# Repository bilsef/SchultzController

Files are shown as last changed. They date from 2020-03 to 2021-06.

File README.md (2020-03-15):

# SchultzController

G-code controller for Siemens S (Schultz) feeders

## Arduino based controller in the hardware section.

The controller board distributes power to the feeders and provides the communication interface for 20 feeder units (40 lanes of components).  There are two versions of the controller board.  The KiCad files are in this folder.
* The 4 pin version has 20 individual 4 pin connectors.  One for each feeder unit.
* the 96 pin version has one 96 pin DIN connector compatible with the connector on the Siemens Communication Unit connector board.  This board is Siemens 1710470-Y1032-C1-01-86 and is inside of 00316265S05.
 
## Arduino code in the firmware section.

The board uses a Arduino Nano Every.  This is a low cost arduino which can easily be soldered to the control board.  Edit the config.h file in the arduino sketch to select the type of board you are using, then upload the sketch to the board.

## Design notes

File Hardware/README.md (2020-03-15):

# Have the board built by JLCPCB.com

* Go to jlcpcb.com and select SMT Assembly->Quote Now.
* Upload the zip file from the CAM directory of the board you want to build.
* Leave everything as default.  Scroll down to SMT Assembly and click Assemble your PCB boards.
* Choose Assemble bottom side.
* Choose your quantity and click Confirm.
* Upload the BOM and POS xlsx files from the CAM directory.
* Click NEXT.
* Confirm the BOM, click NEXT.
* Confirm the parts placement. If the placement doesn't show up, don't worry about it.  It has been verified.  Click SAVE TO CART and complete your purchase.
* [Buy me a coffee](https://www.buymeacoffee.com/cbVmnqB):coffee::smile:
* After you receive your boards, solder on the Arduino Nano Every using the surface mount pads and castellated holes.  Add connectors of your choice.  The 4 pin layout was made for JST B4B-XH-A(LF)(SN) connectors, but any 2.5mm compatible connector should work.

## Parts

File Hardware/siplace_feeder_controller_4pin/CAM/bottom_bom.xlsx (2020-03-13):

Designator | Comment | Footprint | LCSC Part #
Q1 Q2 Q3 Q4 Q5 Q6 Q7 Q8 Q9 Q10 Q11 Q12 Q13 Q14 Q15 Q16 Q17 Q18 Q19 Q20 | BC846 | SOT-23 | C163723
Q21 Q22 Q23 Q24 Q25 Q26 Q27 Q28 Q29 Q30 Q41 Q42 Q43 Q44 Q45 Q46 Q47 Q48 Q49 Q50 | 2N7002 | SOT-23 | C181082
Q60 Q58 Q57 Q56 Q55 Q54 Q53 Q52 Q51 Q31 Q32 Q33 Q34 Q35 Q36 Q37 Q38 Q39 Q40 Q59 | BC856 | SOT-23 | C181145
R1 R2 R3 R4 R5 R6 R7 R8 R9 R10 R11 R12 R13 R27 R28 R29 R30 R31 R32 R33 | 4.7K | R_0603 | C23162
R14 R15 R16 R17 R18 R19 R20 R21 R22 R23 R24 R25 R26 R34 R35 R36 R37 R38 R39 R40 | 330 | R_0603 | C23138
R71 R70 R69 R68 R67 R66 R65 R64 R63 R62 R101 R92 R93 R94 R95 R96 R97 R98 R99 R100 | 1.2K | R_0603 | C22765
R83 R84 R85 R86 R87 R88 R89 R91 R61 R60 R59 R58 R57 R56 R55 R54 R53 R52 R90 R82 | 10K | R_0603 | C25804
R41 | 2.2K | R_0603 | C4190

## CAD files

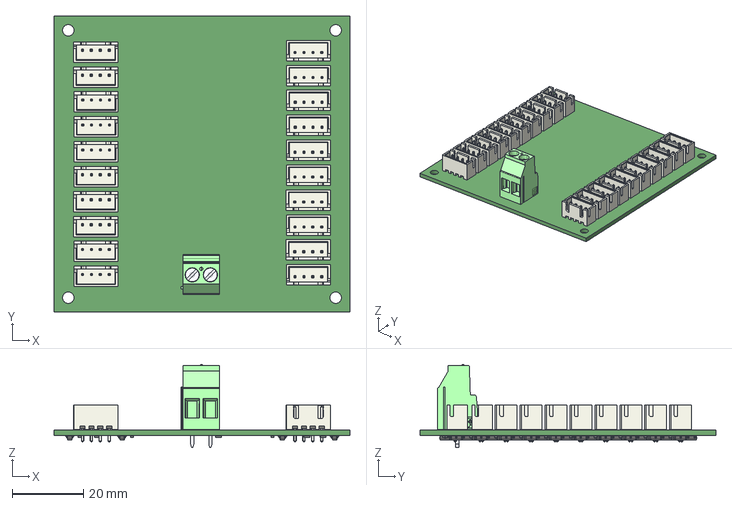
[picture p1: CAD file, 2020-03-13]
Hardware/siplace_feeder_controller_4pin/siplace_feeder_controller.step
83.0 x 83.0 x 23.3 mm

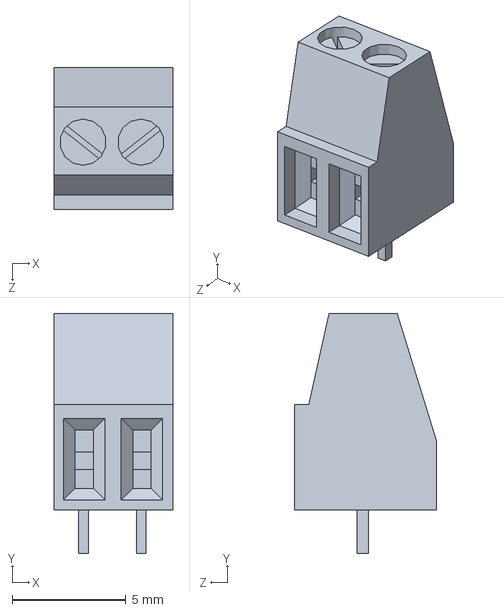
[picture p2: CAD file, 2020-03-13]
Hardware/siplace_feeder_controller_4pin/User Library-Connector-2.SLDPRT
5.22 x 10.5 x 6.22 mm

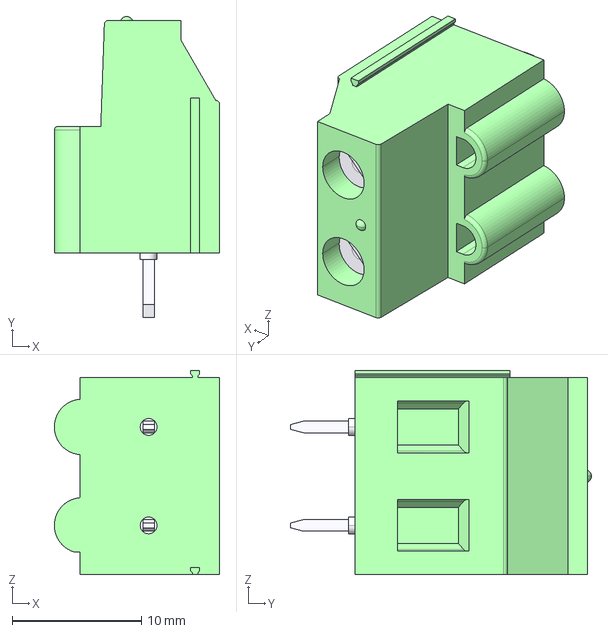
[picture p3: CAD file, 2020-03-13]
Hardware/siplace_feeder_controller_4pin/1732720.stp
12.8 x 23.3 x 15.8 mm

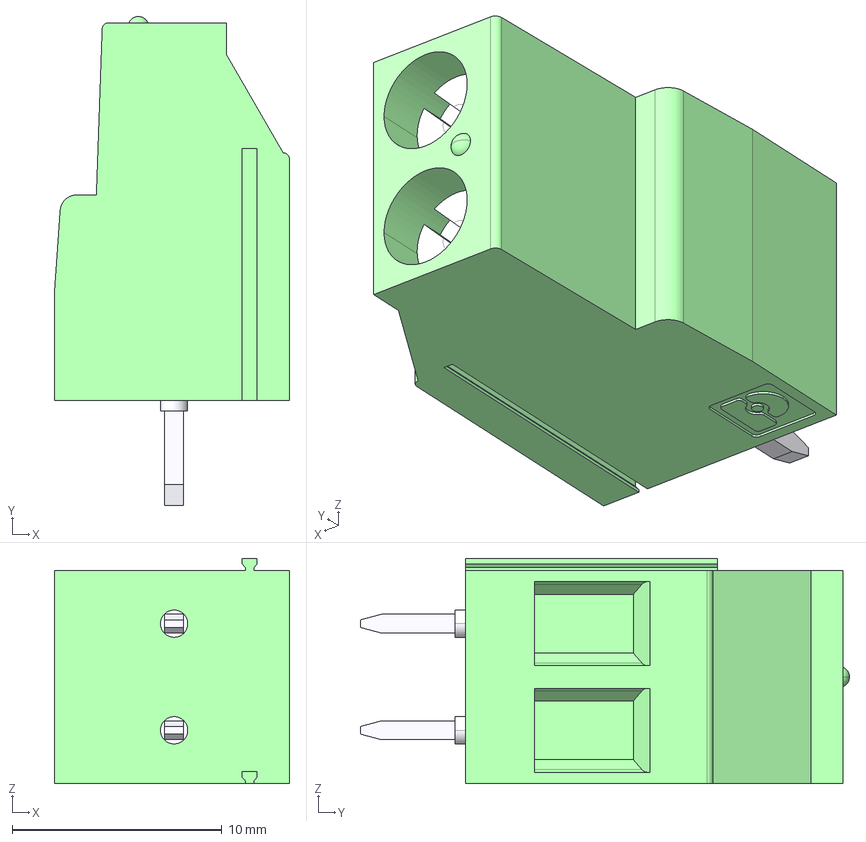
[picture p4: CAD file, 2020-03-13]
Hardware/siplace_feeder_controller_4pin/1706439.stp
11.2 x 23.3 x 10.7 mm

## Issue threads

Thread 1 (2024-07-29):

Compile issue to do library name.

Ccecil, 2024-07-29:
Using Arduino IDE ver. 1.8.19

Error due to missing library named "arduino.h".  Package now named "Arduino.h"

Easy fix but not immediately obvious.

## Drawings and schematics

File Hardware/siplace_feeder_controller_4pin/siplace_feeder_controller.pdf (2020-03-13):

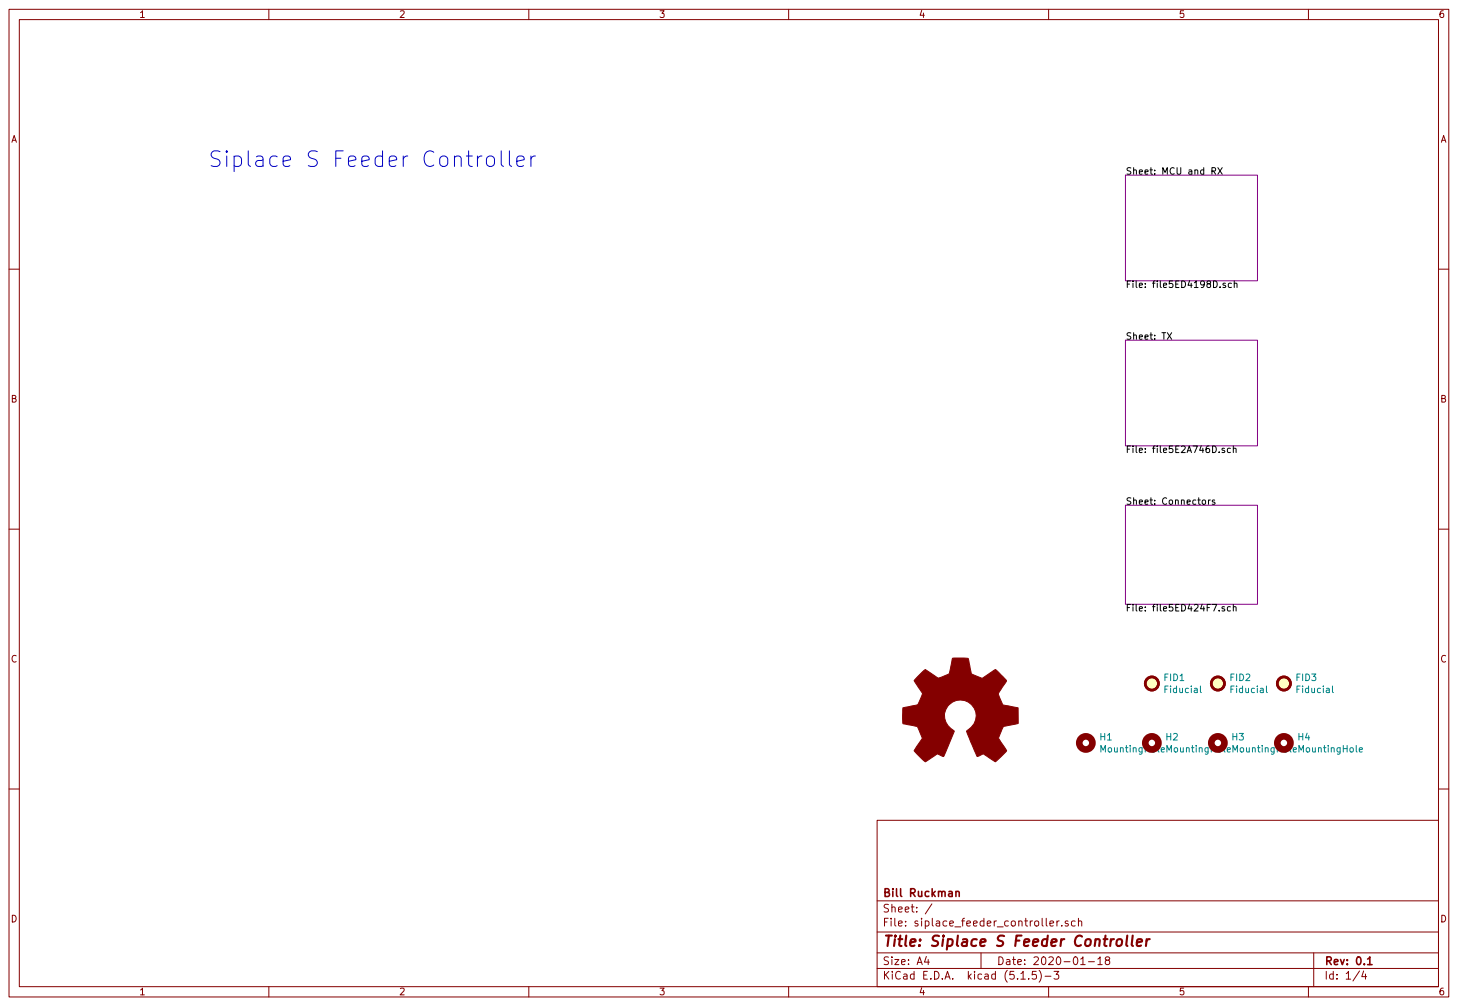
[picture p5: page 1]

Sheet: MCU and RX

File: file5ED4198D.sch Sheet: TX

File: siplace_feeder_controller.sch Sheet: / Bill Ruckman

Id: 1/4 Title: Siplace S Feeder Controller

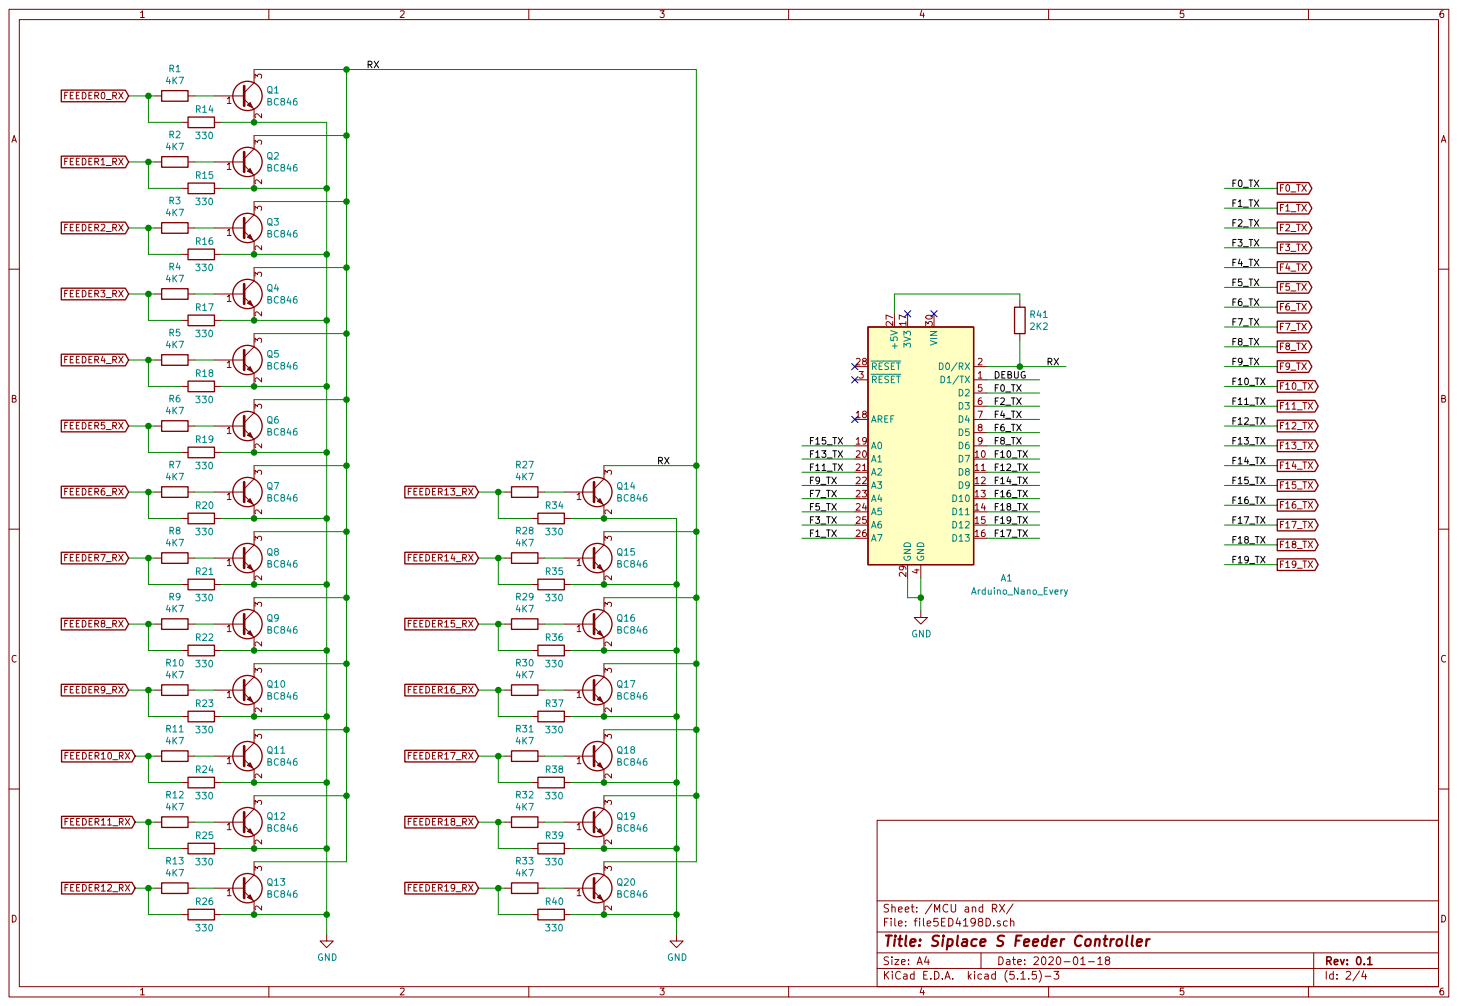
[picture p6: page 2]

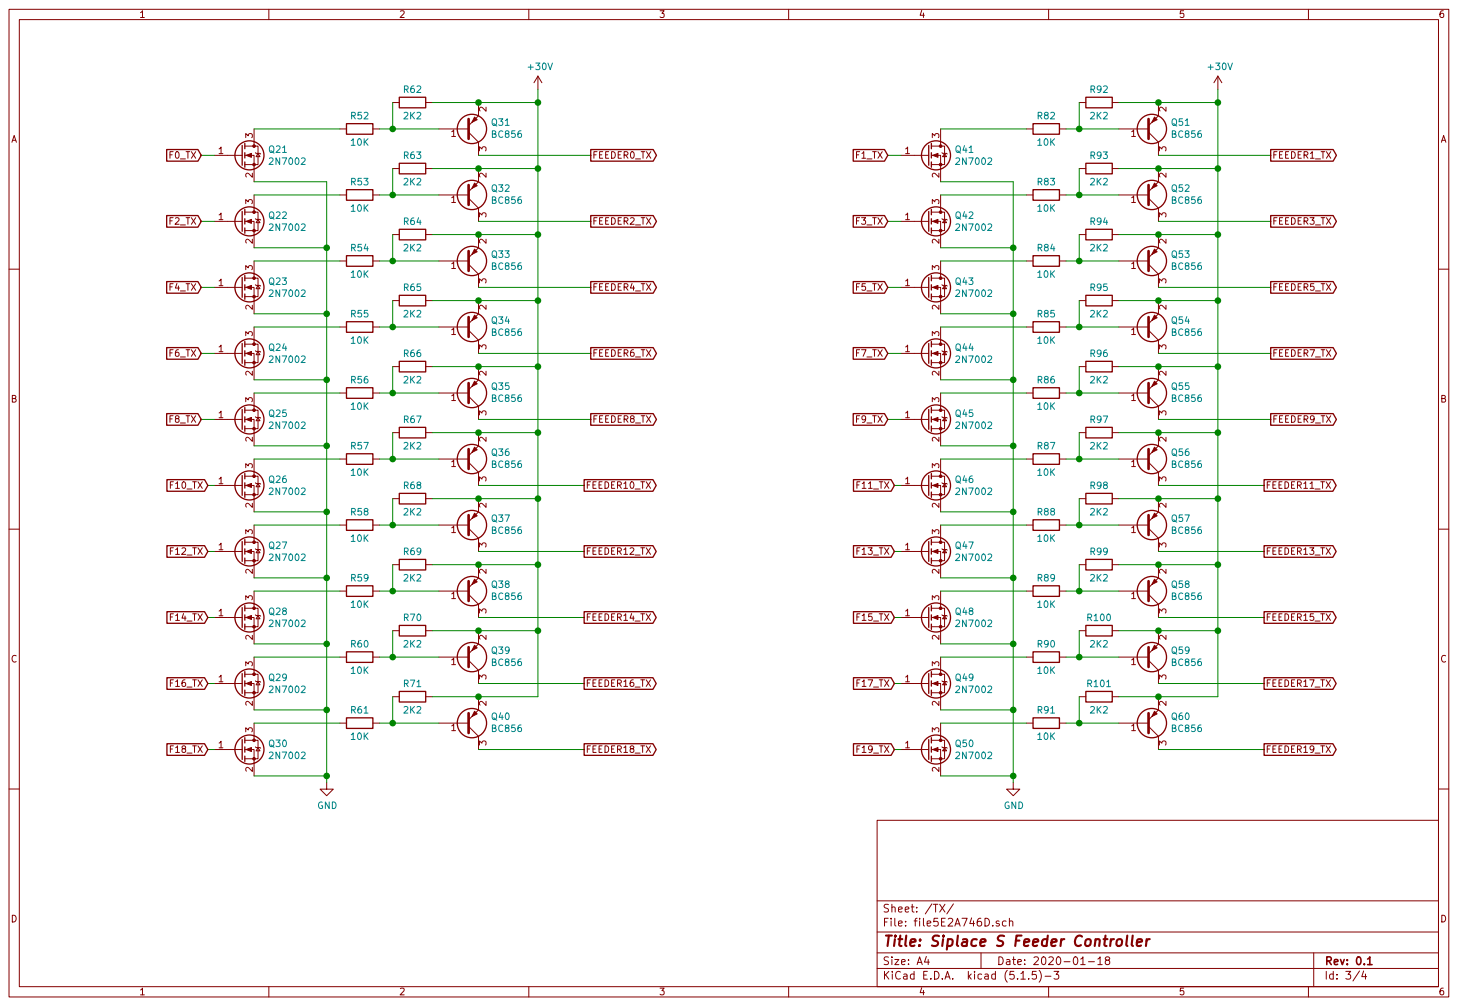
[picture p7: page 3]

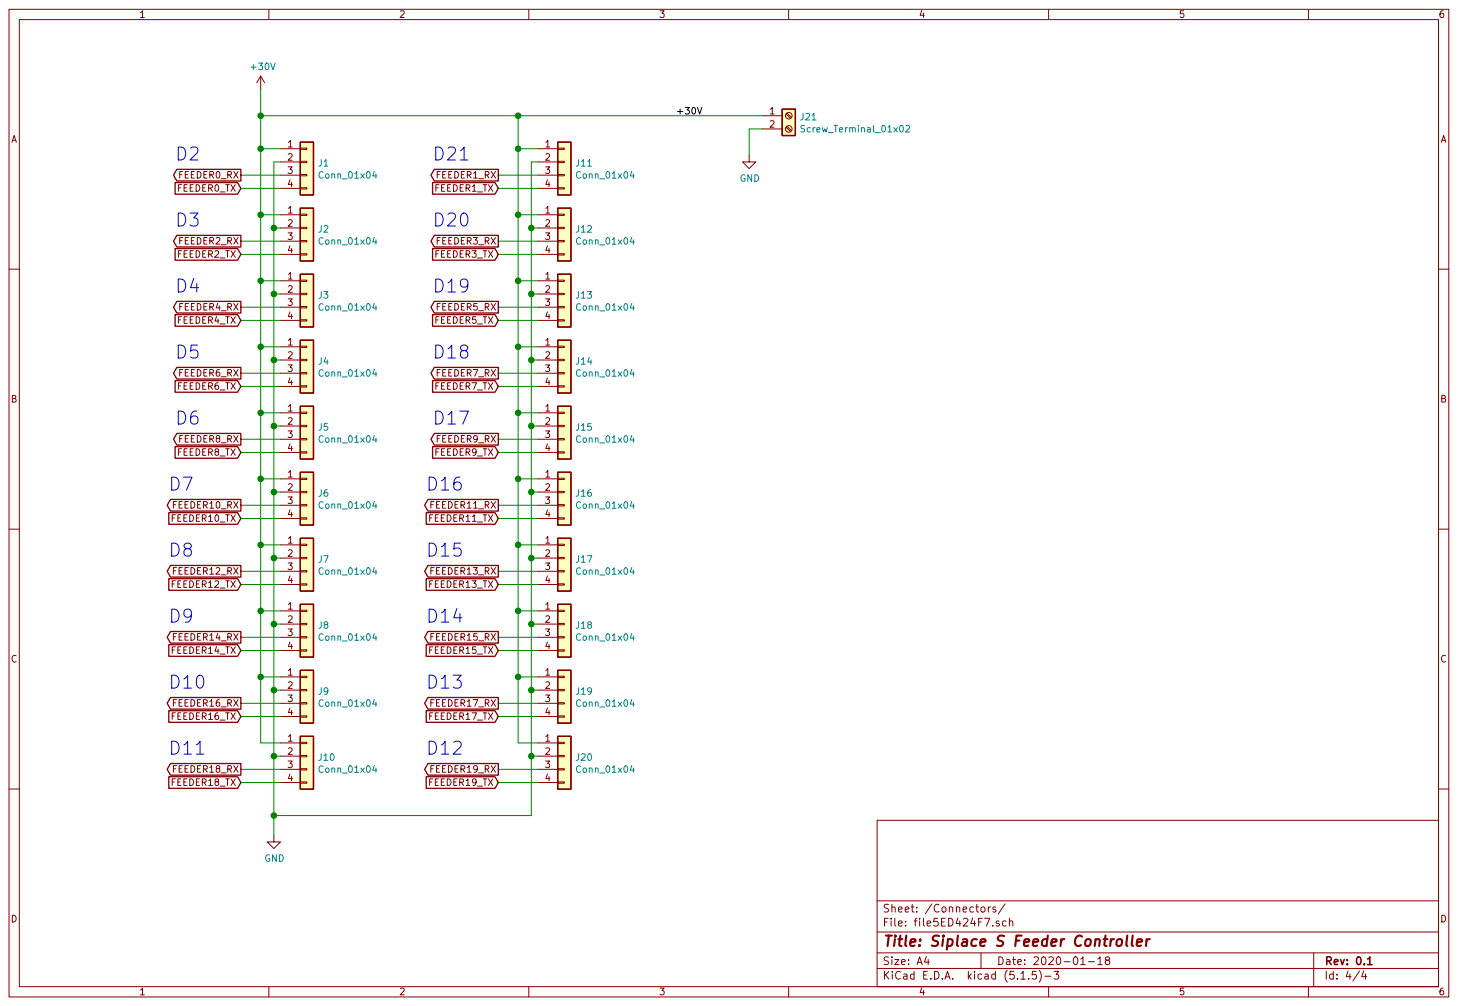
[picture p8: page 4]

Id: 4/4 Title: Siplace S Feeder Controller File: file5ED424F7.sch Sheet: /Connectors/ 1234

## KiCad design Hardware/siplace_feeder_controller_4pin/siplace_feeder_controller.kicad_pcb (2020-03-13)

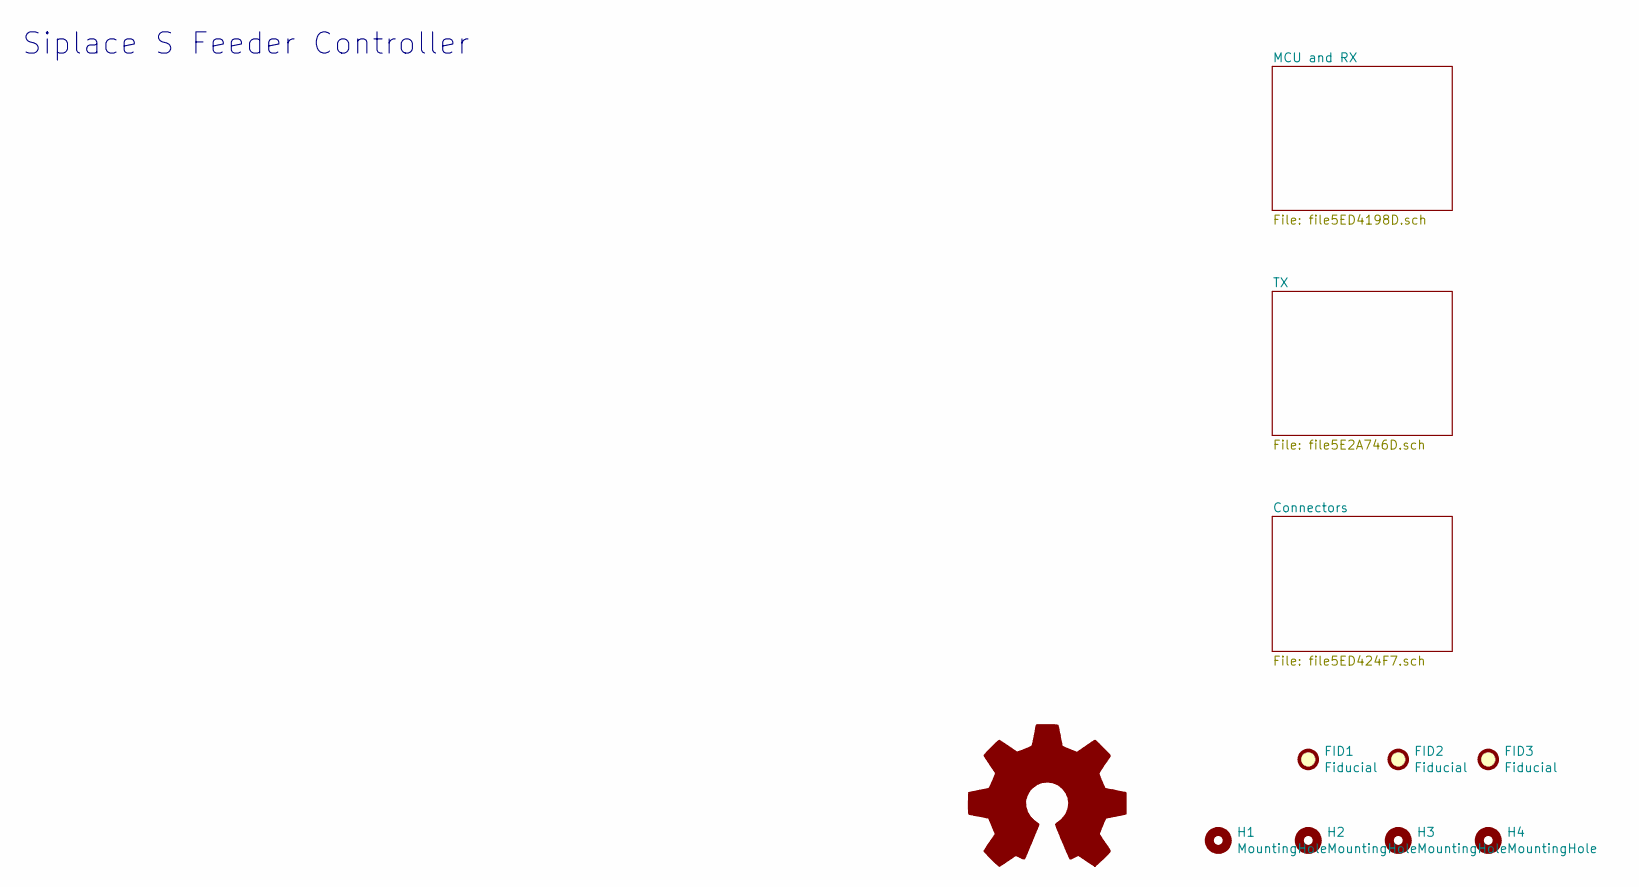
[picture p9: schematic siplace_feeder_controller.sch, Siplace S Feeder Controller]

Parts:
FID1, FID2, FID3: Fiducial; Fiducial_1mm_Mask3mm
H1, H2, H3, H4: MountingHole; MountingHole_3.2mm_M3

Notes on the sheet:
Siplace S Feeder Controller

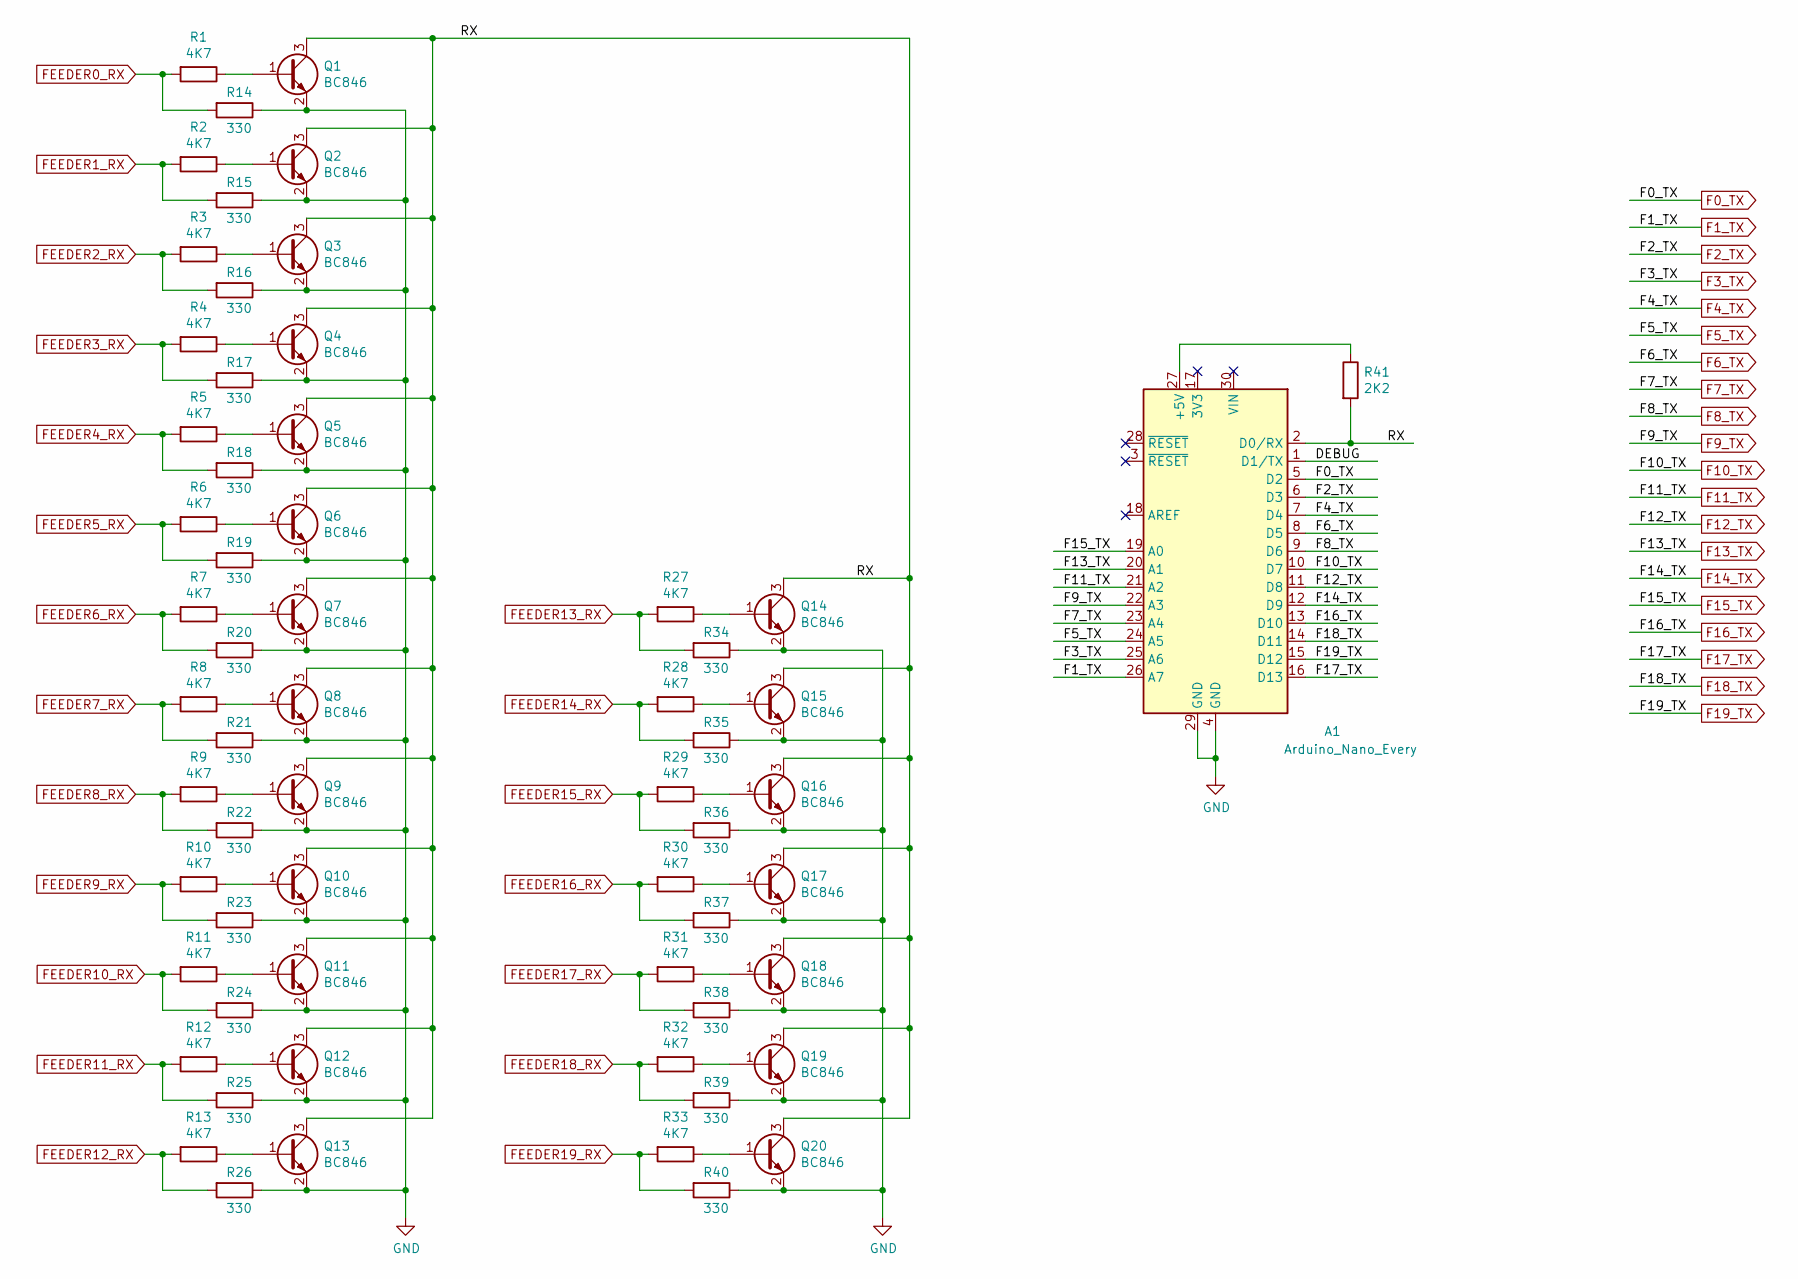
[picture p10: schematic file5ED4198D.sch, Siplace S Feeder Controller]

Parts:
A1: Arduino_Nano_Every; NANO_33_Footprint_SMD_Castell
Q1, Q2, Q3, Q4, Q5, Q6, Q7, Q8, Q9, Q10, Q11, Q12, Q13, Q14, Q15, Q16, Q17, Q18, Q19, Q20: BC846; SOT-23
R1, R2, R3, R4, R5, R6, R7, R8, R9, R10, R11, R12, R13, R27, R28, R29, R30, R31, R32, R33: 4K7; R_0603_1608Metric_Pad1.05x0.95mm_HandSolder
R14, R15, R16, R17, R18, R19, R20, R21, R22, R23, R24, R25, R26, R34, R35, R36, R37, R38, R39, R40: 330; R_0603_1608Metric_Pad1.05x0.95mm_HandSolder
R41: 2K2; R_0603_1608Metric_Pad1.05x0.95mm_HandSolder

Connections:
/MCU and RX/DEBUG: A1.1 (D1/TX)
/MCU and RX/RX: A1.2 (D0/RX), Q1.3 (C), Q2.3 (C), Q3.3 (C), Q4.3 (C), Q5.3 (C), Q6.3 (C), Q7.3 (C), Q8.3 (C), Q9.3 (C), Q10.3 (C), Q11.3 (C), Q12.3 (C), Q13.3 (C), Q14.3 (C), Q15.3 (C), Q16.3 (C), Q17.3 (C), Q18.3 (C), Q19.3 (C), Q20.3 (C), R41.2
F0_TX: A1.5 (D2); also elsewhere on the board
F1_TX: A1.26 (A7); also elsewhere on the board
F2_TX: A1.6 (D3); also elsewhere on the board
F3_TX: A1.25 (A6); also elsewhere on the board
F4_TX: A1.7 (D4); also elsewhere on the board
F5_TX: A1.24 (A5); also elsewhere on the board
F6_TX: A1.8 (D5); also elsewhere on the board
F7_TX: A1.23 (A4); also elsewhere on the board
F8_TX: A1.9 (D6); also elsewhere on the board
F9_TX: A1.22 (A3); also elsewhere on the board
F10_TX: A1.10 (D7); also elsewhere on the board
F11_TX: A1.21 (A2); also elsewhere on the board
F12_TX: A1.11 (D8); also elsewhere on the board
F13_TX: A1.20 (A1); also elsewhere on the board
F14_TX: A1.12 (D9); also elsewhere on the board
F15_TX: A1.19 (A0); also elsewhere on the board
F16_TX: A1.13 (D10); also elsewhere on the board
F17_TX: A1.16 (D13); also elsewhere on the board
F18_TX: A1.14 (D11); also elsewhere on the board
F19_TX: A1.15 (D12); also elsewhere on the board
FEEDER0_RX: R1.2, R14.2; also elsewhere on the board
FEEDER1_RX: R2.2, R15.2; also elsewhere on the board
FEEDER2_RX: R3.2, R16.2; also elsewhere on the board
FEEDER3_RX: R4.2, R17.2; also elsewhere on the board
FEEDER4_RX: R5.2, R18.2; also elsewhere on the board
FEEDER5_RX: R6.2, R19.2; also elsewhere on the board
FEEDER6_RX: R7.2, R20.2; also elsewhere on the board
FEEDER7_RX: R8.2, R21.2; also elsewhere on the board
FEEDER8_RX: R9.2, R22.2; also elsewhere on the board
FEEDER9_RX: R10.2, R23.2; also elsewhere on the board
FEEDER10_RX: R11.2, R24.2; also elsewhere on the board
FEEDER11_RX: R12.2, R25.2; also elsewhere on the board
FEEDER12_RX: R13.2, R26.2; also elsewhere on the board
FEEDER13_RX: R27.2, R34.2; also elsewhere on the board
FEEDER14_RX: R28.2, R35.2; also elsewhere on the board
FEEDER15_RX: R29.2, R36.2; also elsewhere on the board
FEEDER16_RX: R30.2, R37.2; also elsewhere on the board
FEEDER17_RX: R31.2, R38.2; also elsewhere on the board
FEEDER18_RX: R32.2, R39.2; also elsewhere on the board
FEEDER19_RX: R33.2, R40.2; also elsewhere on the board
GND: A1.4 (GND), A1.29 (GND), Q1.2 (E), Q2.2 (E), Q3.2 (E), Q4.2 (E), Q5.2 (E), Q6.2 (E), Q7.2 (E), Q8.2 (E), Q9.2 (E), Q10.2 (E), Q11.2 (E), Q12.2 (E), Q13.2 (E), Q14.2 (E), Q15.2 (E), Q16.2 (E), Q17.2 (E), Q18.2 (E), Q19.2 (E), Q20.2 (E), R14.1, R15.1, R16.1, R17.1, R18.1, R19.1, R20.1, R21.1, R22.1, R23.1, R24.1, R25.1, R26.1, R34.1, R35.1, R36.1, R37.1, R38.1, R39.1, R40.1; also elsewhere on the board
unnamed: A1.27 (+5V), R41.1
unnamed: Q1.1 (B), R1.1
unnamed: Q2.1 (B), R2.1
unnamed: Q3.1 (B), R3.1
unnamed: Q4.1 (B), R4.1
unnamed: Q5.1 (B), R5.1
unnamed: Q6.1 (B), R6.1
unnamed: Q7.1 (B), R7.1
unnamed: Q8.1 (B), R8.1
unnamed: Q9.1 (B), R9.1
unnamed: Q10.1 (B), R10.1
unnamed: Q11.1 (B), R11.1
unnamed: Q12.1 (B), R12.1
unnamed: Q13.1 (B), R13.1
unnamed: Q14.1 (B), R27.1
unnamed: Q15.1 (B), R28.1
unnamed: Q16.1 (B), R29.1
unnamed: Q17.1 (B), R30.1
unnamed: Q18.1 (B), R31.1
unnamed: Q19.1 (B), R32.1
unnamed: Q20.1 (B), R33.1

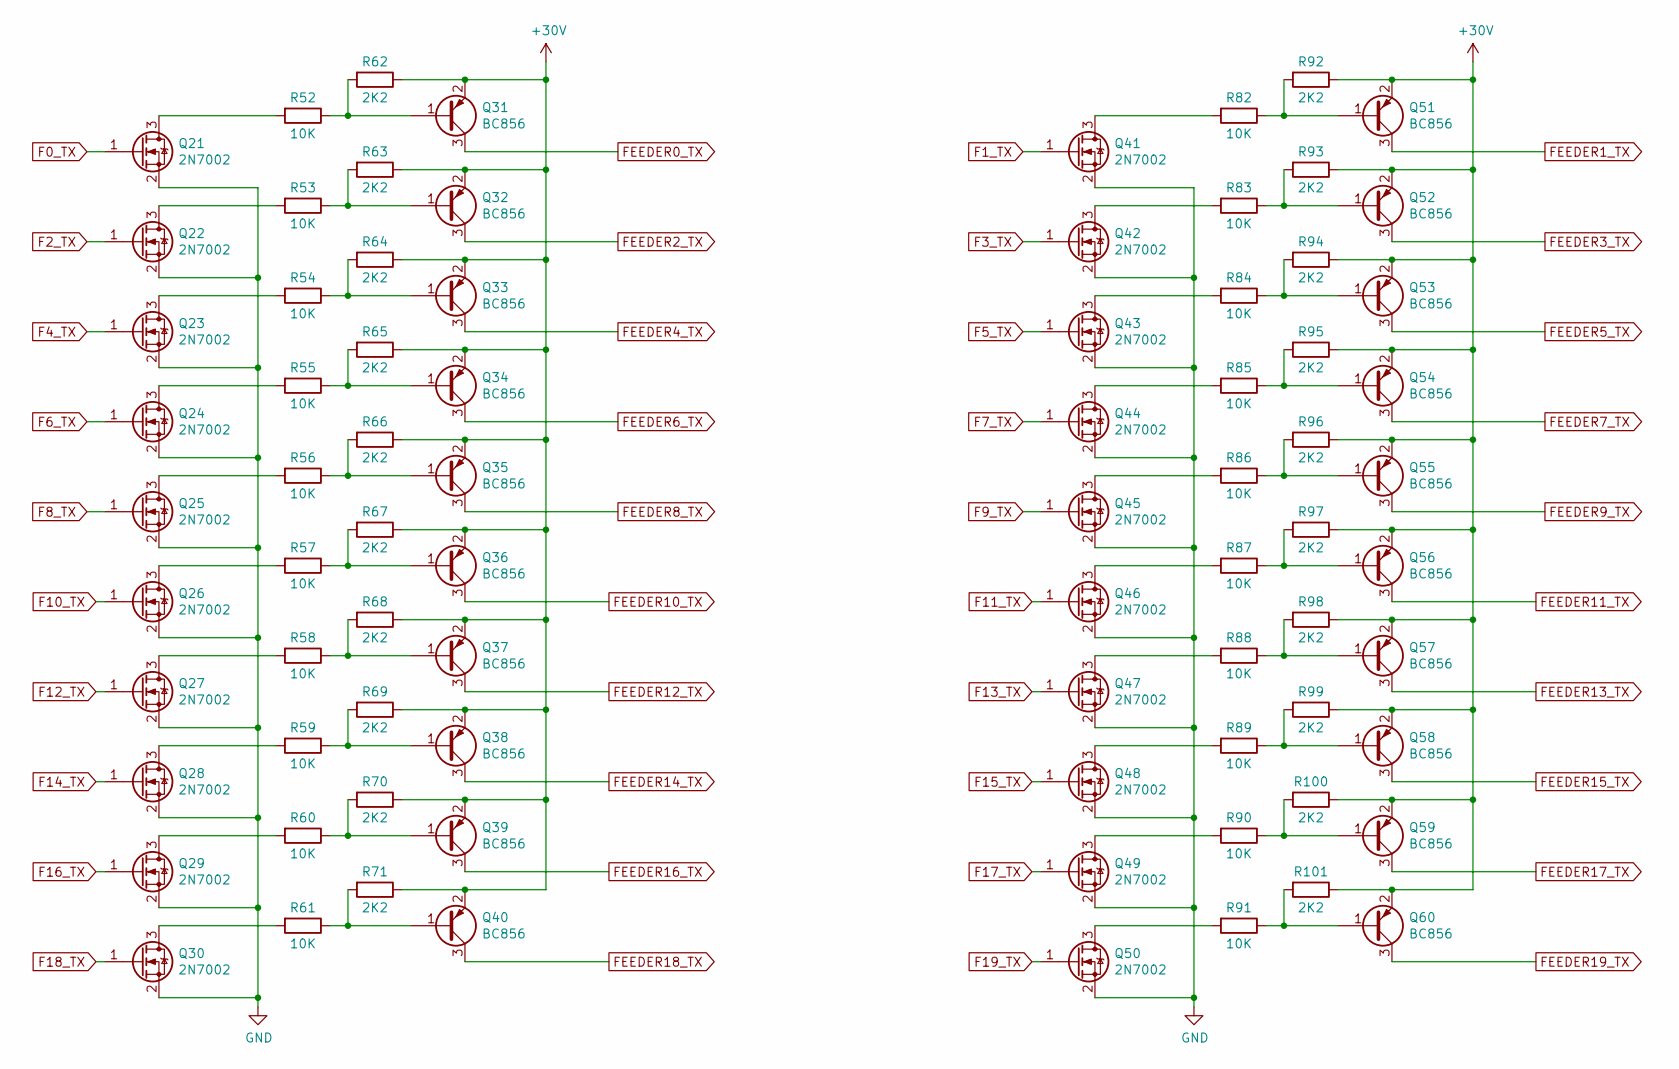
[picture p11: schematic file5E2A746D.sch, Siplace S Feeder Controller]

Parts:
Q21, Q22, Q23, Q24, Q25, Q26, Q27, Q28, Q29, Q30, Q41, Q42, Q43, Q44, Q45, Q46, Q47, Q48, Q49, Q50: 2N7002; SOT-23
Q31, Q32, Q33, Q34, Q35, Q36, Q37, Q38, Q39, Q40, Q51, Q52, Q53, Q54, Q55, Q56, Q57, Q58, Q59, Q60: BC856; SOT-23
R52, R53, R54, R55, R56, R57, R58, R59, R60, R61, R82, R83, R84, R85, R86, R87, R88, R89, R90, R91: 10K; R_0603_1608Metric_Pad1.05x0.95mm_HandSolder
R62, R63, R64, R65, R66, R67, R68, R69, R70, R71, R92, R93, R94, R95, R96, R97, R98, R99, R100, R101: 2K2; R_0603_1608Metric_Pad1.05x0.95mm_HandSolder

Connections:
+30V: Q31.2 (E), Q32.2 (E), Q33.2 (E), Q34.2 (E), Q35.2 (E), Q36.2 (E), Q37.2 (E), Q38.2 (E), Q39.2 (E), Q40.2 (E), Q51.2 (E), Q52.2 (E), Q53.2 (E), Q54.2 (E), Q55.2 (E), Q56.2 (E), Q57.2 (E), Q58.2 (E), Q59.2 (E), Q60.2 (E), R62.1, R63.1, R64.1, R65.1, R66.1, R67.1, R68.1, R69.1, R70.1, R71.1, R92.1, R93.1, R94.1, R95.1, R96.1, R97.1, R98.1, R99.1, R100.1, R101.1; also elsewhere on the board
F0_TX: Q21.1 (G); also elsewhere on the board
F1_TX: Q41.1 (G); also elsewhere on the board
F2_TX: Q22.1 (G); also elsewhere on the board
F3_TX: Q42.1 (G); also elsewhere on the board
F4_TX: Q23.1 (G); also elsewhere on the board
F5_TX: Q43.1 (G); also elsewhere on the board
F6_TX: Q24.1 (G); also elsewhere on the board
F7_TX: Q44.1 (G); also elsewhere on the board
F8_TX: Q25.1 (G); also elsewhere on the board
F9_TX: Q45.1 (G); also elsewhere on the board
F10_TX: Q26.1 (G); also elsewhere on the board
F11_TX: Q46.1 (G); also elsewhere on the board
F12_TX: Q27.1 (G); also elsewhere on the board
F13_TX: Q47.1 (G); also elsewhere on the board
F14_TX: Q28.1 (G); also elsewhere on the board
F15_TX: Q48.1 (G); also elsewhere on the board
F16_TX: Q29.1 (G); also elsewhere on the board
F17_TX: Q49.1 (G); also elsewhere on the board
F18_TX: Q30.1 (G); also elsewhere on the board
F19_TX: Q50.1 (G); also elsewhere on the board
FEEDER0_TX: Q31.3 (C); also elsewhere on the board
FEEDER1_TX: Q51.3 (C); also elsewhere on the board
FEEDER2_TX: Q32.3 (C); also elsewhere on the board
FEEDER3_TX: Q52.3 (C); also elsewhere on the board
FEEDER4_TX: Q33.3 (C); also elsewhere on the board
FEEDER5_TX: Q53.3 (C); also elsewhere on the board
FEEDER6_TX: Q34.3 (C); also elsewhere on the board
FEEDER7_TX: Q54.3 (C); also elsewhere on the board
FEEDER8_TX: Q35.3 (C); also elsewhere on the board
FEEDER9_TX: Q55.3 (C); also elsewhere on the board
FEEDER10_TX: Q36.3 (C); also elsewhere on the board
FEEDER11_TX: Q56.3 (C); also elsewhere on the board
FEEDER12_TX: Q37.3 (C); also elsewhere on the board
FEEDER13_TX: Q57.3 (C); also elsewhere on the board
FEEDER14_TX: Q38.3 (C); also elsewhere on the board
FEEDER15_TX: Q58.3 (C); also elsewhere on the board
FEEDER16_TX: Q39.3 (C); also elsewhere on the board
FEEDER17_TX: Q59.3 (C); also elsewhere on the board
FEEDER18_TX: Q40.3 (C); also elsewhere on the board
FEEDER19_TX: Q60.3 (C); also elsewhere on the board
GND: Q21.2 (S), Q22.2 (S), Q23.2 (S), Q24.2 (S), Q25.2 (S), Q26.2 (S), Q27.2 (S), Q28.2 (S), Q29.2 (S), Q30.2 (S), Q41.2 (S), Q42.2 (S), Q43.2 (S), Q44.2 (S), Q45.2 (S), Q46.2 (S), Q47.2 (S), Q48.2 (S), Q49.2 (S), Q50.2 (S); also elsewhere on the board
unnamed: Q21.3 (D), R52.2
unnamed: Q22.3 (D), R53.2
unnamed: Q23.3 (D), R54.2
unnamed: Q24.3 (D), R55.2
unnamed: Q25.3 (D), R56.2
unnamed: Q26.3 (D), R57.2
unnamed: Q27.3 (D), R58.2
unnamed: Q28.3 (D), R59.2
unnamed: Q29.3 (D), R60.2
unnamed: Q30.3 (D), R61.2
unnamed: Q31.1 (B), R52.1, R62.2
unnamed: Q32.1 (B), R53.1, R63.2
unnamed: Q33.1 (B), R54.1, R64.2
unnamed: Q34.1 (B), R55.1, R65.2
unnamed: Q35.1 (B), R56.1, R66.2
unnamed: Q36.1 (B), R57.1, R67.2
unnamed: Q37.1 (B), R58.1, R68.2
unnamed: Q38.1 (B), R59.1, R69.2
unnamed: Q39.1 (B), R60.1, R70.2
unnamed: Q40.1 (B), R61.1, R71.2
unnamed: Q41.3 (D), R82.2
unnamed: Q42.3 (D), R83.2
unnamed: Q43.3 (D), R84.2
unnamed: Q44.3 (D), R85.2
unnamed: Q45.3 (D), R86.2
unnamed: Q46.3 (D), R87.2
unnamed: Q47.3 (D), R88.2
unnamed: Q48.3 (D), R89.2
unnamed: Q49.3 (D), R90.2
unnamed: Q50.3 (D), R91.2
unnamed: Q51.1 (B), R82.1, R92.2
unnamed: Q52.1 (B), R83.1, R93.2
unnamed: Q53.1 (B), R84.1, R94.2
unnamed: Q54.1 (B), R85.1, R95.2
unnamed: Q55.1 (B), R86.1, R96.2
unnamed: Q56.1 (B), R87.1, R97.2
unnamed: Q57.1 (B), R88.1, R98.2
unnamed: Q58.1 (B), R89.1, R99.2
unnamed: Q59.1 (B), R90.1, R100.2
unnamed: Q60.1 (B), R91.1, R101.2

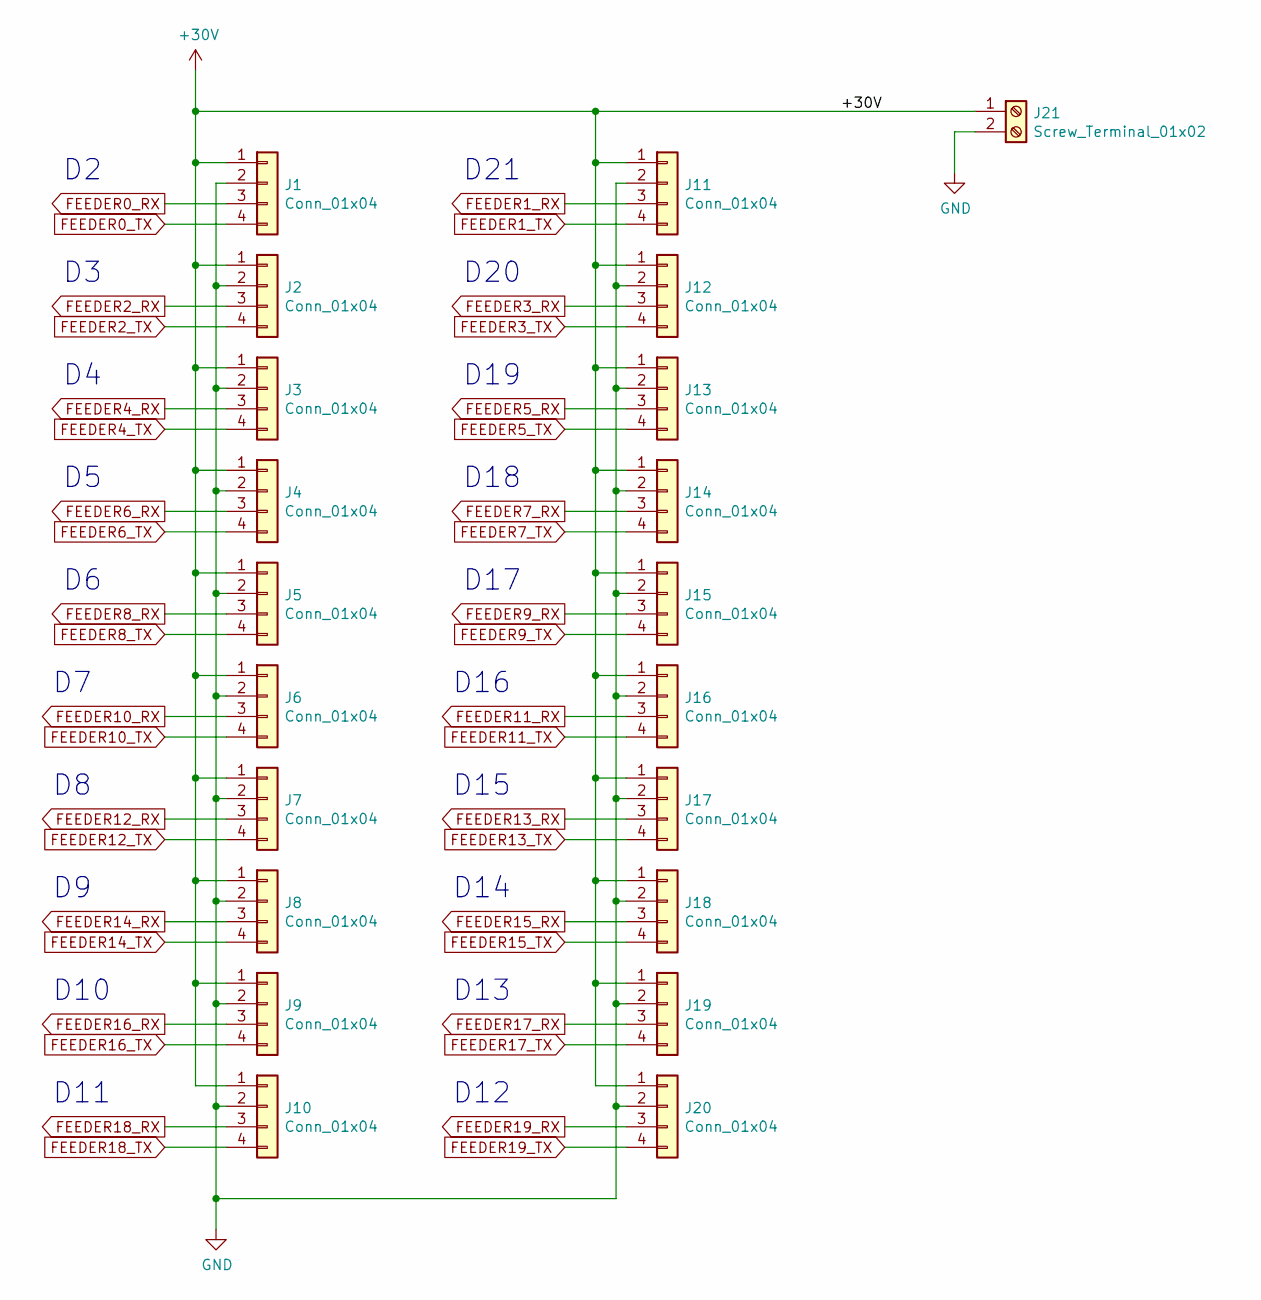
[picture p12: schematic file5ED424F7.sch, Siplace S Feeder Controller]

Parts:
J1, J2, J3, J4, J5, J6, J7, J8, J9, J10, J11, J12, J13, J14, J15, J16, J17, J18, J19, J20: Conn_01x04; JST_XH_B4B-XH-A_1x04_P2.50mm_Vertical
J21: Screw_Terminal_01x02; TerminalBlock_Phoenix_MKDS-1,5-2-5.08_1x02_P5.08mm_Horizont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

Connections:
+30V: J1.1, J2.1, J3.1, J4.1, J5.1, J6.1, J7.1, J8.1, J9.1, J10.1, J11.1, J12.1, J13.1, J14.1, J15.1, J16.1, J17.1, J18.1, J19.1, J20.1, J21.1; also elsewhere on the board
FEEDER0_RX: J1.3; also elsewhere on the board
FEEDER0_TX: J1.4; also elsewhere on the board
FEEDER1_RX: J11.3; also elsewhere on the board
FEEDER1_TX: J11.4; also elsewhere on the board
FEEDER2_RX: J2.3; also elsewhere on the board
FEEDER2_TX: J2.4; also elsewhere on the board
FEEDER3_RX: J12.3; also elsewhere on the board
FEEDER3_TX: J12.4; also elsewhere on the board
FEEDER4_RX: J3.3; also elsewhere on the board
FEEDER4_TX: J3.4; also elsewhere on the board
FEEDER5_RX: J13.3; also elsewhere on the board
FEEDER5_TX: J13.4; also elsewhere on the board
FEEDER6_RX: J4.3; also elsewhere on the board
FEEDER6_TX: J4.4; also elsewhere on the board
FEEDER7_RX: J14.3; also elsewhere on the board
FEEDER7_TX: J14.4; also elsewhere on the board
FEEDER8_RX: J5.3; also elsewhere on the board
FEEDER8_TX: J5.4; also elsewhere on the board
FEEDER9_RX: J15.3; also elsewhere on the board
FEEDER9_TX: J15.4; also elsewhere on the board
FEEDER10_RX: J6.3; also elsewhere on the board
FEEDER10_TX: J6.4; also elsewhere on the board
FEEDER11_RX: J16.3; also elsewhere on the board
FEEDER11_TX: J16.4; also elsewhere on the board
FEEDER12_RX: J7.3; also elsewhere on the board
FEEDER12_TX: J7.4; also elsewhere on the board
FEEDER13_RX: J17.3; also elsewhere on the board
FEEDER13_TX: J17.4; also elsewhere on the board
FEEDER14_RX: J8.3; also elsewhere on the board
FEEDER14_TX: J8.4; also elsewhere on the board
FEEDER15_RX: J18.3; also elsewhere on the board
FEEDER15_TX: J18.4; also elsewhere on the board
FEEDER16_RX: J9.3; also elsewhere on the board
FEEDER16_TX: J9.4; also elsewhere on the board
FEEDER17_RX: J19.3; also elsewhere on the board
FEEDER17_TX: J19.4; also elsewhere on the board
FEEDER18_RX: J10.3; also elsewhere on the board
FEEDER18_TX: J10.4; also elsewhere on the board
FEEDER19_RX: J20.3; also elsewhere on the board
FEEDER19_TX: J20.4; also elsewhere on the board
GND: J1.2, J2.2, J3.2, J4.2, J5.2, J6.2, J7.2, J8.2, J9.2, J10.2, J11.2, J12.2, J13.2, J14.2, J15.2, J16.2, J17.2, J18.2, J19.2, J20.2, J21.2; also elsewhere on the board

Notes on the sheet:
D21
D10
D11
D20
D19
D18
D17
D16
D15
D14
D13
D12

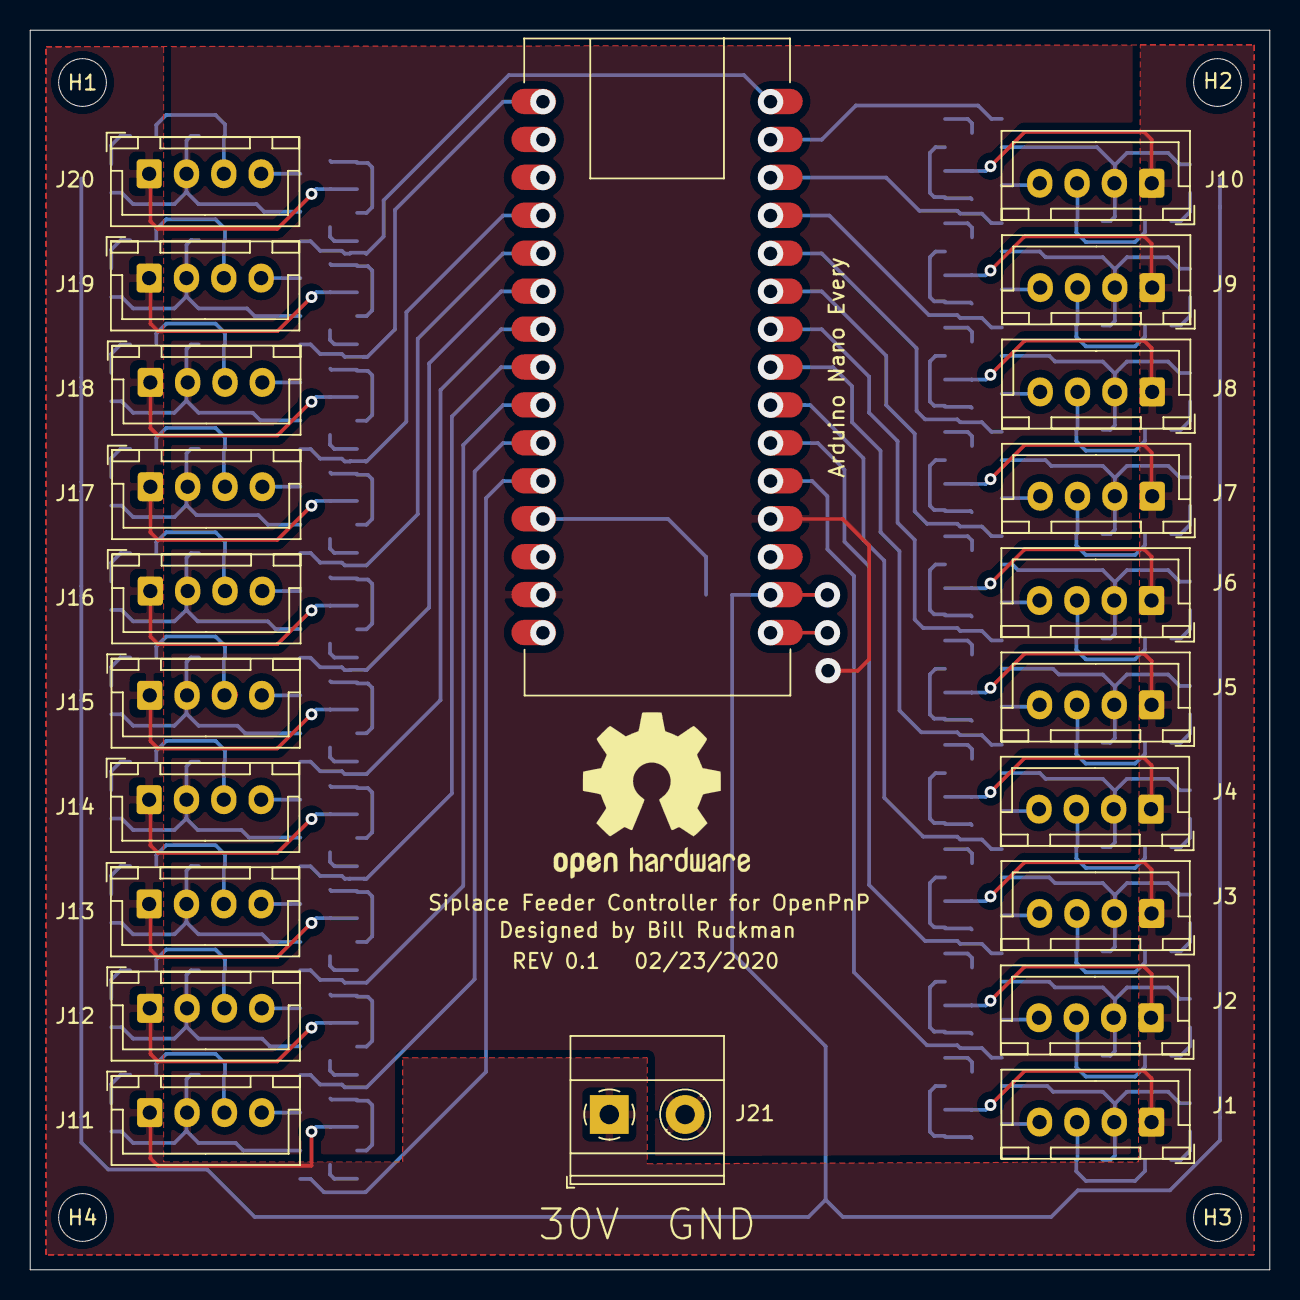
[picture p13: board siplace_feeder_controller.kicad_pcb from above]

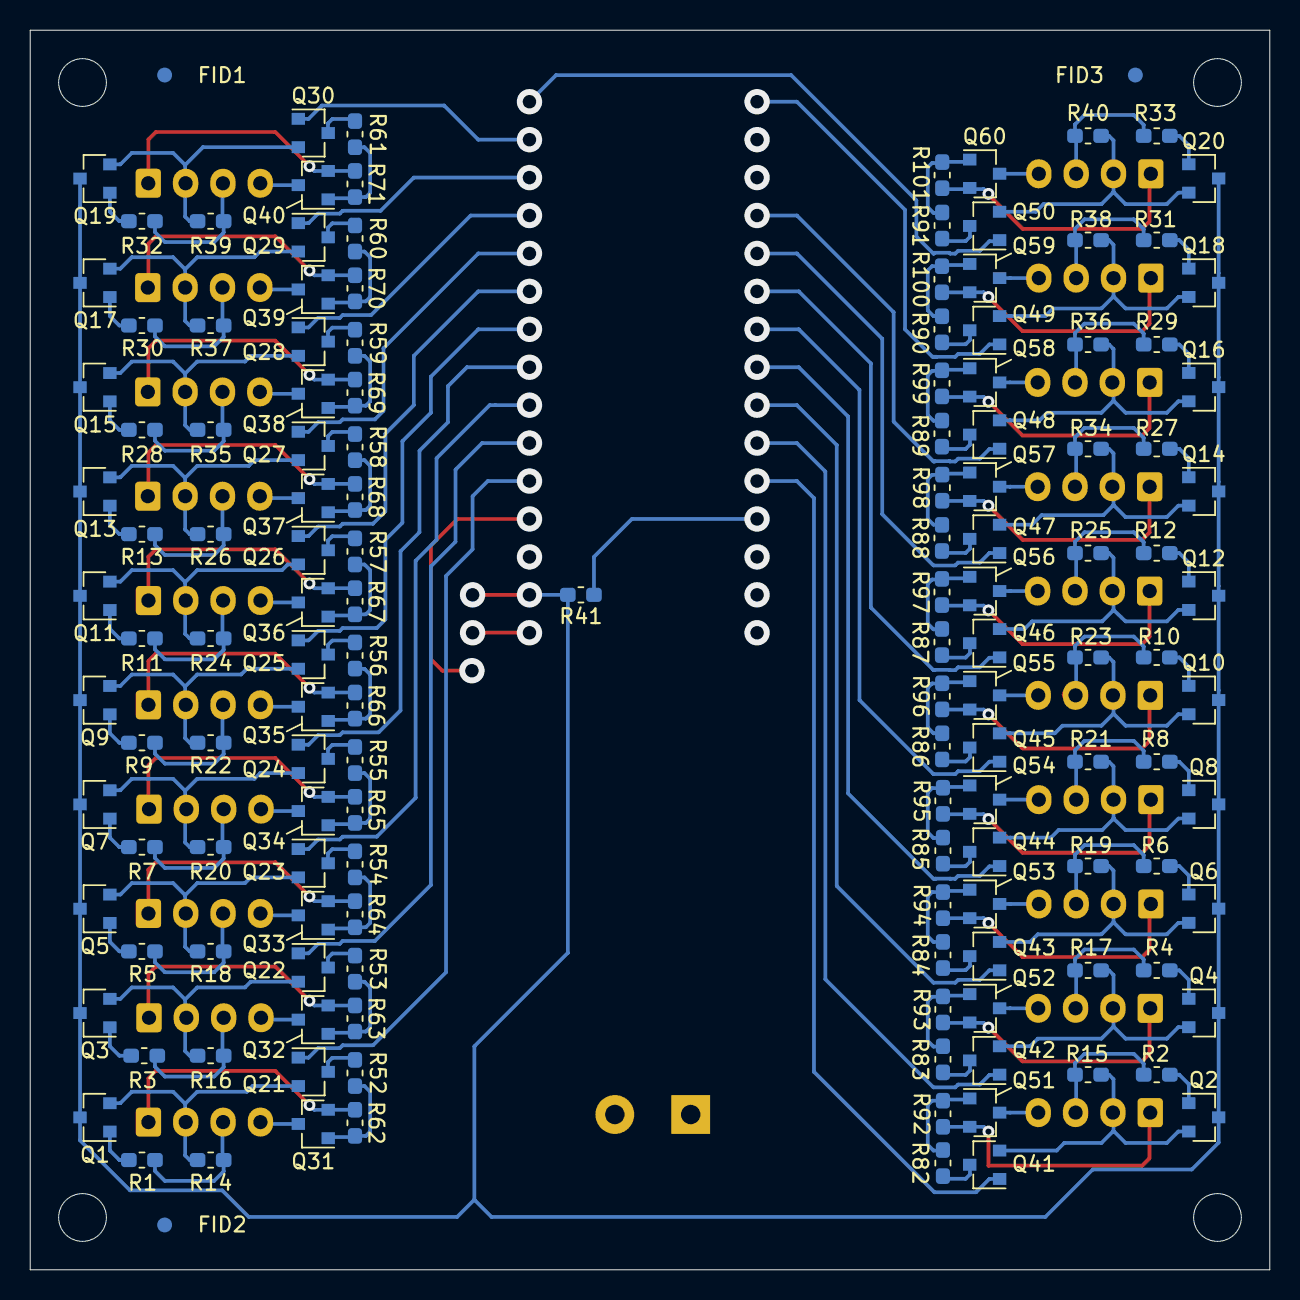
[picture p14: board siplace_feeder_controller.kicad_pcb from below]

Board: 2 copper layers, 83.0 x 83.0 mm, 170 parts (144 on the bottom side), 124 nets.

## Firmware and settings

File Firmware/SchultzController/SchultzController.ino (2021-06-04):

/*
* Author: Bill Ruckman
* (c)2020
*
* Adapted from 0816feeder by mrgl
*    https://github.com/mgrl/0816-feeder-firmware
*
* This work is licensed under a Creative Commons Attribution-NonCommercial-ShareAlike 4.0 International License.
* http://creativecommons.org/licenses/by-nc-sa/4.0/
*
* current version: v0.0
*
*
*/

// ------------------  I N C  L I B R A R I E S ---------------

#include "config.h"
#include "Feeder.h"


// ------------------  V A R  S E T U P -----------------------

FeederClass feeders[NUMBER_OF_FEEDERS];

// ------------------  U T I L I T I E S ---------------


// ------------------  S E T U P -----------------------
void setup() {
  byte i;
  
	Serial.begin(SERIAL_BAUD);
	while (!Serial);
	Serial.println("Controller starting..."); Serial.flush();
	
	Serial1.begin(9600); // The hardware RX port
  
  for (i = 0; i < NUMBER_OF_FEEDERS; i++) {
    feeders[i].setup(i, i/LANES_PER_PORT, i%LANES_PER_PORT);	// initialize with feeder number, port and lane
  }
  
	// setup listener to serial stream
	setupGCodeProc();

	Serial.println("Controller ready.");

}



// ------------------  L O O P -----------------------

void loop() {
	// Process incoming serial data and perform callbacks
	listenToSerialStream();

}

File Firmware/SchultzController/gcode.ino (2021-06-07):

#include "config.h"

String inputBuffer[] = {"", "", "", ""};         // Buffer for incoming G-Code lines
int bufPtr = 0;

/**
* Look for character /code/ in the inputBuffer and read the float that immediately follows it.
* @return the value found.  If nothing is found, /defaultVal/ is returned.
* @input code the character to look for.
* @input defaultVal the return value if /code/ is not found.
**/
float parseParameter(String inBuf, char code, float defaultVal) {
	int codePosition = inBuf.indexOf(code);
	if(codePosition!=-1) {
		//code found in buffer

		//find end of number (separated by " " (space))
		int delimiterPosition = inBuf.indexOf(" ",codePosition+1);

		float parsedNumber = inBuf.substring(codePosition+1,delimiterPosition).toFloat();

		return parsedNumber;
		} else {
		return defaultVal;
	}

}

void setupGCodeProc() {
  for (int i=0; i<4; i++) {
	  inputBuffer[i].reserve(MAX_BUFFFER_MCODE_LINE);
  }
}

void sendAnswer(uint8_t error, String message) {
  switch (error) {
    case 0: {
      Serial.print("ok ");
      Serial.println(message);
      break;
    }

    case 1: {
      Serial.print("error ");
      Serial.println(message);
      break;
    }

    case 2: {
      Serial.println(message);
      Serial.println("ok ");
      break;
    }
  }
}

bool validFeederNo(int8_t signedFeederNo, uint8_t feederNoMandatory = 0) {
	if(signedFeederNo == -1 && feederNoMandatory >= 1) {
		//no number given (-1) but it is mandatory.
		return false;
		} else {
		//state now: number is given, check for valid range
		if(signedFeederNo<0 || signedFeederNo>(NUMBER_OF_FEEDERS-1)) {
			//error, number not in a valid range
			return false;
			} else {
			//valid number
			return true;
		}
	}
}

bool validPitch(int8_t pitch, uint8_t pitchMandatory = 0) {
  if(pitch == -1 && pitchMandatory >= 1) {
    //no number given (-1) but it is mandatory.
    return false;
    } else {
    //state now: number is given, check for valid range
    if(pitch<0 || pitch>1) {
      //error, number not in a valid range
      return false;
      } else {
      //valid number
      return true;
    }
  }
}

bool validFeederID(int32_t signedFeederID, uint8_t feederIDMandatory = 0) {
  if(signedFeederID == -1 && feederIDMandatory >= 1) {
    //no number given (-1) but it is mandatory.
    return false;
    } else {
    //state now: number is given, check for valid range
    if(signedFeederID<0 || signedFeederID>65535) {
      //error, number not in a valid range
      return false;
      } else {
      //valid number
      return true;
    }
  }
}

/**
* Read the input buffer and find any recognized commands.  One G or M command per line.
*/
void processCommand(String cmdBuf) {

	//get the command, default -1 if no command found
	int cmd = parseParameter(cmdBuf, 'M', -1);

	#ifdef DEBUG
	Serial.print("command found: M");
	Serial.println(cmd);
	#endif


	switch(cmd) {

    // M115
    case MCODE_DRIVER_INFO: {
      sendAnswer(2,"FIRMWARE_NAME: Schultz Feeder Controller, FIRMWARE_VERSION: 2.0");
      break;
    }

		/*
		FEEDER-CODES
		*/

		case MCODE_PRE_PICK: {

			int8_t signedFeederNo = (int)parseParameter(cmdBuf, 'N',-1);

			//check for presence of a mandatory FeederNo
			if(!validFeederNo(signedFeederNo,1)) {
				sendAnswer(1,"feederNo missing or invalid");
				break;
			}

			//send pre pick command
			if (!feeders[signedFeederNo].sendPrePick()) {
				sendAnswer(1,"No acknowledge from feeder");
			} else {
				sendAnswer(0,"Shutter opened");
			}
     
      break;
		}

		case MCODE_ADVANCE: {
			int8_t signedFeederNo = (int)parseParameter(cmdBuf, 'N',-1);
			int8_t overrideErrorRaw = (int)parseParameter(cmdBuf, 'X',-1);
			bool overrideError = false;
			if(overrideErrorRaw >= 1) {
				overrideError = true;
				#ifdef DEBUG
				Serial.println("Argument X1 found, error will be ignored");
				#endif
			}

			//check for presence of a mandatory FeederNo
			if(!validFeederNo(signedFeederNo,1)) {
				sendAnswer(1,"feederNo missing or invalid");
				break;
			}

			//send feed command
			if (!feeders[signedFeederNo].sendAdvance(overrideError)) {
				sendAnswer(1,"Unable to advance tape");
			} else {
				sendAnswer(0,"Tape advanced");
			}
			
			break;
		}

		case MCODE_FEEDER_STATUS: {
			int8_t signedFeederNo = (int)parseParameter(cmdBuf, 'N',-1);

			//check for presence of FeederNo
			if(!validFeederNo(signedFeederNo,1)) {
				sendAnswer(1,"feederNo missing or invalid");
				break;
			}

			sendAnswer(0,feeders[signedFeederNo].reportStatus());

			break;
		}

		case MCODE_GET_FEED_COUNT: {
			int8_t signedFeederNo = (int)parseParameter(cmdBuf, 'N',-1);

			//check for presence of FeederNo
			if(!validFeederNo(signedFeederNo,1)) {
				sendAnswer(1,"feederNo missing or invalid");
				break;
			}

      uint8_t inBuf[24];
			if(feeders[signedFeederNo].readEEPROM(inBuf)) {
        uint32_t counth = inBuf[5];
        counth <<= 16;
        uint32_t countm = inBuf[3];
        countm <<= 8;
        uint32_t count = counth + countm + inBuf[2];
        char countStr[22];
        sprintf(countStr, "Feed count: %lu", count);
  			sendAnswer(0,countStr);
      } else {
        sendAnswer(1," no response from feeder");
      }

			break;
		}

		case MCODE_CLEAR_FEED_COUNT: {
			int8_t signedFeederNo = (int)parseParameter(cmdBuf, 'N',-1);

			//check for presence of FeederNo
			if(!validFeederNo(signedFeederNo,1)) {
				sendAnswer(1,"feederNo missing or invalid");
				break;
			}

			if (!feeders[signedFeederNo].clearFeedCount()) {
				sendAnswer(1,"Unable to clear feed count");
			} else {
				sendAnswer(0,"Feed count cleared");
			}

			break;
		}

    case MCODE_GET_ERR42_COUNT: {
      int8_t signedFeederNo = (int)parseParameter(cmdBuf, 'N',-1);

      //check for presence of FeederNo
      if(!validFeederNo(signedFeederNo,1)) {
        sendAnswer(1,"feederNo missing or invalid");
        break;
      }

      uint8_t inBuf[24];
      if(feeders[signedFeederNo].readEEPROM(inBuf)) {
        uint16_t count = inBuf[12] & 0x0f;
        count <<= 8;
        count += inBuf[8];
        char countStr[22];
        sprintf(countStr, "Error 42 count: %u", count);
        sendAnswer(0,countStr);
      } else {
        sendAnswer(1," no response from feeder");
      }

      break;
    }

    case MCODE_GET_ERR43_COUNT: {
      int8_t signedFeederNo = (int)parseParameter(cmdBuf, 'N',-1);

      //check for presence of FeederNo
      if(!validFeederNo(signedFeederNo,1)) {
        sendAnswer(1,"feederNo missing or invalid");
        break;
      }

      uint8_t inBuf[24];
      if(feeders[signedFeederNo].readEEPROM(inBuf)) {
        uint16_t count = inBuf[12] & 0xf0;
        count <<= 4;
        count += inBuf[9];
        char countStr[22];
        sprintf(countStr, "Error 43 count: %u", count);
        sendAnswer(0,countStr);
      } else {
        sendAnswer(1," no response from feeder");
      }

      break;
    }
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

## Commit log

2020-02-23 Update
    Add new gcodes and rearrange numbers.
    Change port numbers for 96 pin connector version.
2020-03-02 Add ability to set pitch from GUI
2020-03-08 Fix bug where setting pitch was corrupting EEPROM
    Fix bug where setting pitch was corrupting EEPROM.
    Add command to set ID and initialize EEPROM.
    [Feeder.cpp, Feeder.h, gcode.ino]
2020-03-13 Added hardware files
    [1706439.stp, 1732720.stp, DIN Pinout.xlsx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]
2020-03-13 Update CAM files
    [siplace_feeder_controller-B_Cu.gbl, siplace_feeder_controller-B_Mask.gbs, siplace_feeder_controller-B_Paste.gbp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]
2020-03-13 remove extraneous files
    [siplace_feeder_controller_adapter-Edge_Cuts.gm1, siplace_feeder_controller_adapter-bottom-pos.xlsx]
2020-03-13 file clean-up
    [DIN Pinout.xlsx, bottom_bom.xlsx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]
2021-06-04 Removed F() macro calls
    Latest IDE failed to compile for Nano Every
    [Feeder.cpp, SchultzController.ino, gcode.ino]
2021-06-06 Fix formatting of M115 message
    [gcode.ino]
2021-06-13 Update AlignFeeders.js
    Skip slots that do not have a feeder loaded.
